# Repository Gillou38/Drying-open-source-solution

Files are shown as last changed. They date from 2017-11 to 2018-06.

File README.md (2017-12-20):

Open Source Vegetable Dryer
===========================

-   A vegetable dryer 

-   Combines solar and electrical energies

-   Designed for professional farmers

-   Scalable and autonomous

Motivation
----------

### Why this project?

This project is dedicated to farmers needing drying solutions for their
vegetables, aromatic or medicinal plants, fruits or other kinds of products. The
drying process allows farmers spreading their outcome beyond the harvest season
and therefore to secure a stable revenue over the year.

### Why open source?

We concur with the idea that open source and DIY farming tools support technical
independence, which is a critical issue for farmers. Therefore, dryer we want to
develop here is aimed to be open source, to be produced indifferently in DIY or
industrial production settings, and to be easily repaired. we are committed to
provide technical solutions with sufficient documentation securing the four
freedoms of open source:

-   Freedom to study: the right to access enough information to understand how
    the piece of hardware (referred herein as the product) works and to retrace
    the logic behind its design;

-   Freedom to modify: the right to edit the product definition documents and to
    tweak or develop the product further for any purpose;

-   Freedom to make: the right to use the product definition documents to
    manufacture the piece of hardware;

-   Freedom to distribute: the right to share or sell the product definition
    documents as well as the physical products fabricated according to these
    documents.

The documentation shared in this repository is licensed under a [GNU GPL v3
license](http://www.gnu.de/documents/gpl.en.html). Designs are licensed under a
[CERN Open Hardware Licence
V1.2](https://www.ohwr.org/licenses/cern-ohl/license_versions/v1.2).

### How to contribute

Every bit of help is more than welcomed. If you want to support the project,
promote it or concretely participate in the development, have a look at our
[Contribution
guide](https://github.com/Gillou38/Drying-open-source-solution/blob/master/Contribution%20guide.md)!

About dry-ing and -ers
----------------------

Drying is one of the most efficient food conservation methods. It helps keeping
a great share of nutriment, reduces the weight and the volume of food products
and enables long warehousing duration. It is a physicochemical reaction, whose
aim is to extract water out of something. Professional alimentary applications
requires dealing with conflicting constraints of high processing speed and
keeping control on the reaction in order to conserve valuable nutriments.

### History
That technic begins with the beginning of the agriculture, around 12 000 B. C. by inhabitants of the modern Middle East and Asia region. In beginning drying was realize by evaporation (air drying, sun drying ...). With time and technical evolution, there's actually a lot of different technic to dry food, from very low tech solution to high tech solution (we exclude freezing drying, because it's a very different process).

In drying, there is no “one-size-fits-all”-solution. Each farmer may need a very
specific solution fitting their specific requirements regarding size and
temperature range for example. The objective of the project is therefore to
develop a scalable and modular dryer which can be adapted to each specific
situation. Doing so, we want also to provide documentation about drying which
can be easily accessible to farmers.

### Composition of a dryer

A dryer is composed of:

-   a drying room, whose aim is to host the food products to be dried and to put
    their surface in contact with a dry and heated airflow. The role of the air
    flow is to capture the water contained in the food products while getting in
    contact with their surface. In order to maximise the contact surface, a good
    solution is to use trays helping to distribute the products and let the
    airflow circulating around them. Trays are generally made of food-safe
    screens and frameworks. For drying aromatic and medicinal plants, there are
    generally two ways to distribute products on the trays: the “thin layer”-way
    with only one layer of product on each tray, and the “thick layer”-way with
    around 10 to 15 centimetres of products on each tray.

-   a heating system, which can either be solar (direct or indirect), electrical
    or fuelled by biomass or combustion.

-   an air flow drying system, which can be either based on air exchange,
    condensation or absorption.

-   a convection system to convey the dry air flow through the drying room. The
    choice of the convection system depends on the product to be dried, the
    expected drying time and the thickness of the food's layer. It can be either
    natural or forced.

-   optionally a thermal inertia system, helping dryers whose heating system
    can't operate all day long (like solar systems) to stock energy.

Basic dryers tend to combine functions such as drying and heating into one
component and to use wind to create ventilation. More advanced solutions use one
component for each function.

Our design rationale
--------------------
We intend to use low tech and low energy consumption solutions whenever it is
possible. The current development focuses on a solar solution with electrical
assistance and regulation which enable professional users to process food
products regardless of the daytime (that is, even when there is no sunlight).

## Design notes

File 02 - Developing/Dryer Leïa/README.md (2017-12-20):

Dryer Model “Leïa”
==================

Specifications
--------------

Initial requirements

-   to dry 80kg of fresh herbs per week

-   drying time 2.5 days

-   40kg workload

-   thick layer loading (4 kg/m²)

Derived requirements

-   10m² drying surface

-   21 drawers of about 0,48m² (0,6\*0,8)

Materials
---------

-   Flat structures: resin-less OSB (oriented strand board)

-   Beams: pine

-   Drawer bottom: cheese maturing canvas

Supporting structure
---------

- Section: 50 x 50 mm
  
- No structure on the front side to tread drawers

- Fix together with angle connector

Drawers
-------

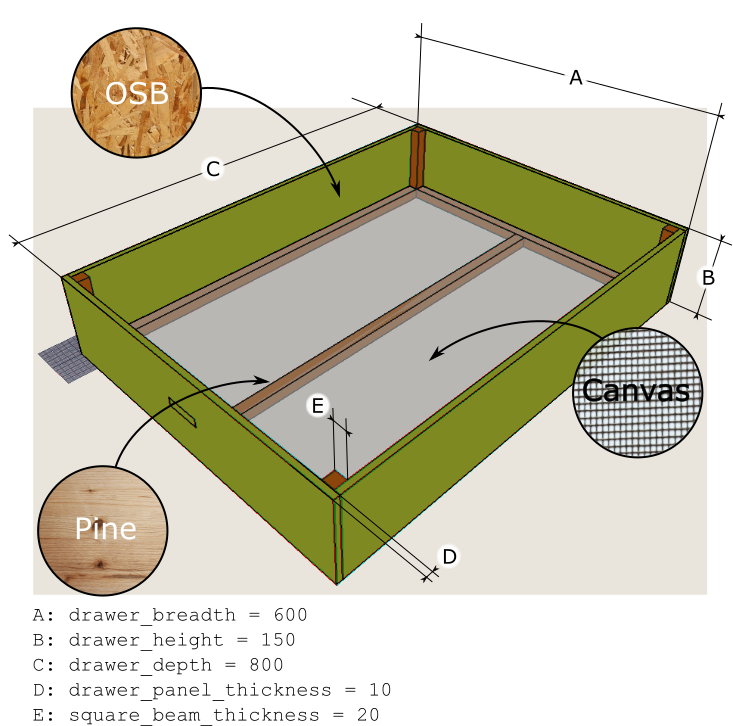
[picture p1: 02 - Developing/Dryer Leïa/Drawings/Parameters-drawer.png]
Drawer parameter sketch


Supporting structure
---------

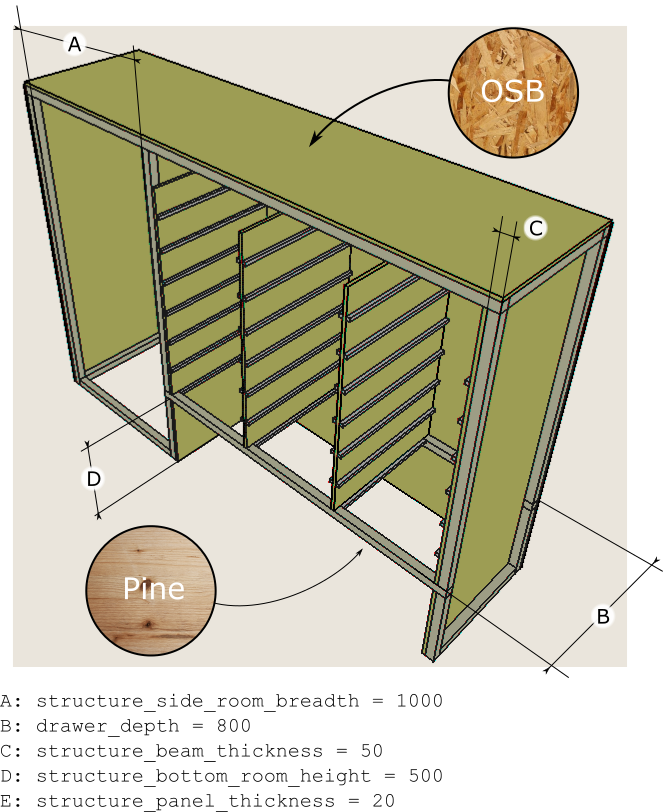
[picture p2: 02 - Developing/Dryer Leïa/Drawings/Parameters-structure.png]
Structure parameter sketch


Layout structure
---------

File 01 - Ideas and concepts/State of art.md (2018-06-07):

# State of art
#test
For basics category, we inspire by *“Les séchoirs solaires – Théorie et pratique”* de Michel Daguenet, because he made a huge work about drying science, and more applied to solar drying.

# Summary
## [Dryer for solid, centimetre scale](https://github.com/Gillou38/Drying-open-source-solution/blob/master/01%20-%20Ideas%20and%20concepts/State%20of%20art.md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)

### [Convective Dryer](https://github.com/Gillou38/Drying-open-source-solution/blob/master/01%20-%20Ideas%20and%20concepts/State%20of%20art.md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)

[1 Global parameter](https://github.com/Gillou38/Drying-open-source-solution/blob/master/01%20-%20Ideas%20and%20concepts/State%20of%20art.md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)

[2 Drying room](https://github.com/Gillou38/Drying-open-source-solution/blob/master/01%20-%20Ideas%20and%20concepts/State%20of%20art.md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)

[3 Suupling system](https://github.com/Gillou38/Drying-open-source-solution/blob/master/01%20-%20Ideas%20and%20concepts/State%20of%20art.md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)

[4 Heat source](https://github.com/Gillou38/Drying-open-source-solution/blob/master/01%20-%20Ideas%20and%20concepts/State%20of%20art.md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)

[5 Convection system](https://github.com/Gillou38/Drying-open-source-solution/blob/master/01%20-%20Ideas%20and%20concepts/State%20of%20art.md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)

[6 Automation](https://github.com/Gillou38/Drying-open-source-solution/blob/master/01%20-%20Ideas%20and%20concepts/State%20of%20art.md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)

[7 Alimentary legislation](https://github.com/Gillou38/Drying-open-source-solution/blob/master/01%20-%20Ideas%20and%20concepts/State%20of%20art.md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)

# Dryer for solid, centimetre scale
That part relate to drying of: 
- plants
- vegetables
- fruits
- nuts
- cheese
- mushroom
- more ?

For all that kind of food goods the process is almost the same, it use the same components (exept for cheese which doesn't need heating), only parameters change (temperature, time, relative humidity ...)

We try to make an inventory of all kind of dryer, and technology which could be used to dry, from the convective drying to the freeze drying, and defined each technology (electric, solar ...) used in each kind of dryers. For the 2nd level of category (convective, Freeze, IR, microwave) we choose to class them by kind of technology. Maybe, we can found a best classification.

## Convective drying
Convective drying consist of a contact between food goods and an heat and dry airflow to deshumidify food goods. It the most common process using for small products, because it's the cheaper and simpler process.

### 1. Global parameters
There is a lot of different kind of dryer, from the little dryer for domestic application to the huge dryer for industrial application, there can be organized in one block, or in some blocks, which make a more modulare system. 

#### A. Size
Actually we can’t precisely defined size in function of application, it depends of the food goods.
##### - Domestic
That’s kind of dryer could be used by a single man/women or a family for their own food.

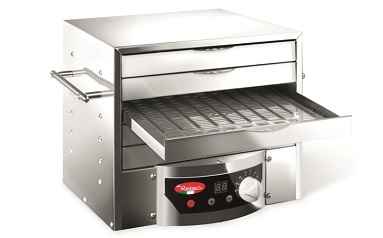
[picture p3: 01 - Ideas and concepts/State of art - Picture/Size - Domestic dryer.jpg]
Domestic dryer


##### - Little production
That size of dryer, is adapted to little company, people which want to sell product at local market.

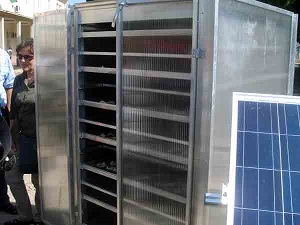
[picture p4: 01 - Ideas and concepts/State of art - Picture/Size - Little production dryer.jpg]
Little production dryer


##### - Industrial production
Dryer adapted for industrial production, sell product in large region.

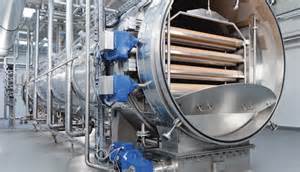
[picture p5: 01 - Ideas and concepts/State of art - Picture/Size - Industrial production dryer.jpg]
Industrial dryer


#### B. Organization
#####  - Mono-bloc
That kind of organisation could be a compact organization (like a multi-bloc organization hook together) or an all in drying room organization.

Advantages:
- easy to make, no pipe to link each part
- compact

Disadvantages:
- not transportable for middle size (size of a big wardrobe) of dryer

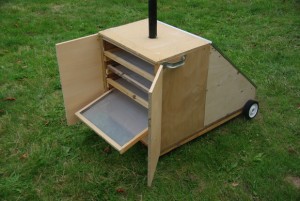
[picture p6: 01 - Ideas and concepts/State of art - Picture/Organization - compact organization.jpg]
Compact organization
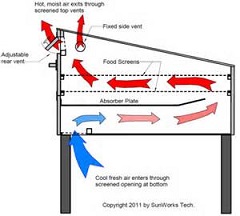
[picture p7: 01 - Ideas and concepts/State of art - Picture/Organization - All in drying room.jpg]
All in drying room
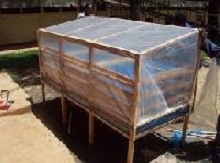
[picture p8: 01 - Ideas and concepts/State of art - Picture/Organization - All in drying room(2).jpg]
All in drying room (2)
           

#####   - Multi-bloc
Advantages:
- can be move by part, maybe can be taken apart (démonté)
- modulability

Disadvantages: 
- lost energy (temperature and airflow) in pipe

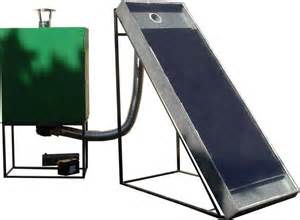
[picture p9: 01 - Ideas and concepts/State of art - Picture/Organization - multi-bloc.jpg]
Multi-bloc


#### C. Transportable
##### 1) Fixed
We don’t imaged that kind of dryer because it could defined by a very large panel of dryer. So we consider in that category all dryer which can’t be transport by 2 or less humans.
##### 2) Transportable
#####   - Portable
Defined by little dryer, which integrate handle or part which can be considered like handle, and which can be transport by maximum 2 peoples.

Portable

#####   - Pliable
The same restriction than a “portable” dryer, which pliable part to make an easy to transport dryer when it necessary.

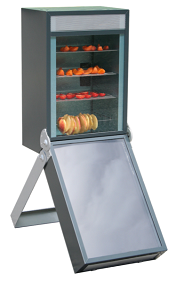
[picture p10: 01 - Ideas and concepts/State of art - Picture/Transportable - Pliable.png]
Pliable


#####   - Wheel
Dryer which integrate one or more wheel to transport it.

big one
2 Wheels

### 2. Drying room
#### A. Materials
We don't find European restriction for indirect contact, like it appear with drying room in a dryer. In that case, food goods can stay in the same room during few days with the same air, so we consider indirect contact like direct contact, we work later more presicely about that question. Maybe restriction could be simplified if the dryer work with renewable air.
(See under for more precision)

#### - Stone – Building:
Dryer directly integrate in a building. It can vary from old building (like an attic) to modern building with waxed concrete. For that part, we need to study food grade materials to identified what kind of material could be used, almost sure waxed concrete is legal, the rest need more study.

We think than, for nuts and that kind of fruit, dryer don't need to be totally clean, but for other kind of products building have to be really clean. 

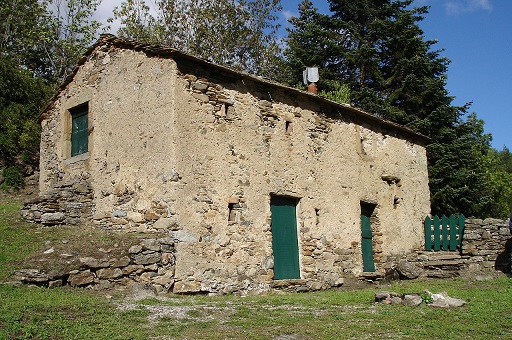
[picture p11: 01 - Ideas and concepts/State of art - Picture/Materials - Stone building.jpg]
Traditional nuts dryer


#### - Steel
Steel is a good solution for fruits and vegetables dryers, which need to be wash with water after each utilization, so stainless steel is easy to clean and it's resilient.

*[French source](http://www.contactalimentaire.com/index.php?id=204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)*

Stainless dryer

#### - Wood:
Wood is easiest material to make by oneself, but it doesn't work to any solutions, like with humid product (see under) which need to clean drying room with food grade cleaning product.

Wood dryer

#### - Plastic
Plastic is a good solution for fruits and vegetables dryers, which need to be wash with water after each utilization, so plastic is easy to clean but it isn't resilient.

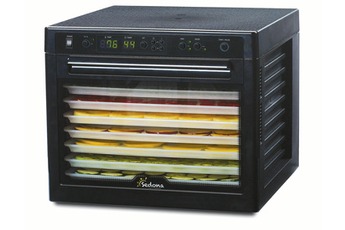
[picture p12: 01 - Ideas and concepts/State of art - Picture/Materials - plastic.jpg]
Plastic dryer


#### - Varnish materials
What kind of varnish could be used, what the maximum rate of product could be used.

- Vanish for wood
For fruit and vegetable dryers which need to be clean with water, wood without vanish can't reply to that restriction. So to vanish wood could be a great solution to have an easy to make dryer and respect very restricted alimentary regulation.

#### - cleaning products
You need to clean materials and objects, which could be in contact with food goods, before each using.

#### B. Shape
That the very hard part of the state of art, a lot of forms of dryer was experiment since the first realisation 12 000 years before, so we try to make the most complete list of kind of dryer, to inspire us and other to during the design of there dryer.
Maybe some dryers which can be regroup in the same category but to be sure to list all kind of dryer, we separate all little difference.
#### - Shell type (indirect solar natural convection)

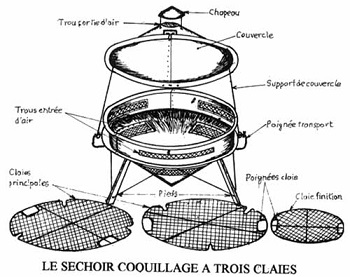
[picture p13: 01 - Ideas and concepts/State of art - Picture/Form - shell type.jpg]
Shell Type


#### - Vertical type with trays

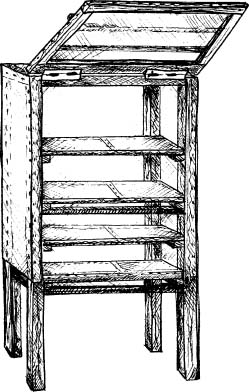
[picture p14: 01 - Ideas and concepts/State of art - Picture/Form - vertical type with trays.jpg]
Vertical with trays


#### - Spread type (solar direct):
Spread dryer, is a special form of vertical dryer, adapt to solar direct application, but it can be used in different case but that’s not real useful.

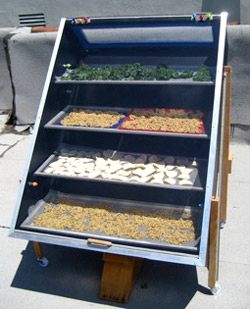
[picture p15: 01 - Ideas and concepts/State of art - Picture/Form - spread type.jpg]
Spread type


#### - Tunnel type
That’s more or less the same system than spread type, but for that category we exclude direct solar input. So, all kind of heat source could be considered. 

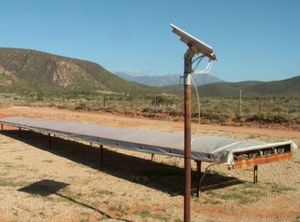
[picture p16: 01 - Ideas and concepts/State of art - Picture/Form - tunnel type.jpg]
Tunnel type
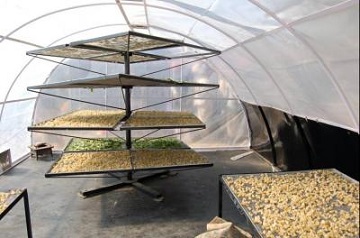
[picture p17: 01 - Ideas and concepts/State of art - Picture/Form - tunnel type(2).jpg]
Tunnel type(2)
     

#### - Rotative cylinder type
More adapted for cereals, and that kind of products. That kind of dryer is composed of a rotative drying room, which is crossed by an airflow. It provide to dry equitably all products. It doesn't need trays, but it need an high level of complexity. It more adapted for industrial applications.

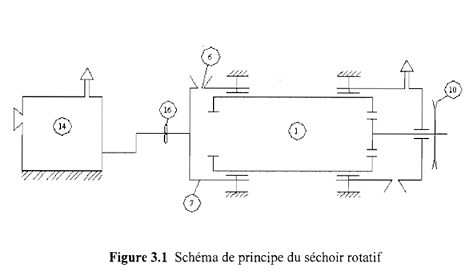
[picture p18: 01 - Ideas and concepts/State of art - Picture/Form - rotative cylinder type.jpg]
Rotative cylinder type
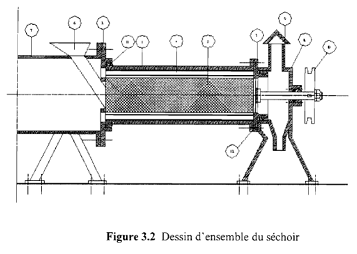
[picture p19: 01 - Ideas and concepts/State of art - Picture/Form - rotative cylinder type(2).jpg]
Rotative cylinder type
     

#### - Silo type

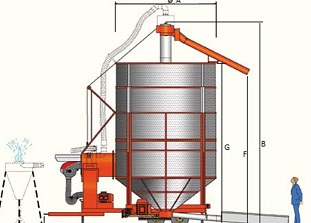
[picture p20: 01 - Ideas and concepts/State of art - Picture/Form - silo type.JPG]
Silo type


#### - Screw dryer type

screw dryer type

#### 3 Supplying systems
#### 3.1 Containing systems
Trays is the most using system to display product for artisanal or industrial application (exept for industrial drying of cereals), but other systems could be used in different applications.

For example, people who just want to dry some plants suspend bunch in an hot room ...

#### 3.1.1 Loosely

##### 3.1.1.1 Reversal
##### - Screw 
See [Screw dryer](http://www.amb-rousset.com/products/sechoir-a-vis/) or [another dryer](http://www.heinkel.com/products/dryers-and-mixers/conical-screw-vacuum-dryer.aspx)

##### 3.1.1.2 Not reversal

##### - Cylindric contener - Silo
Silo type

##### - Square contener - Bac

square contener

#### 3.1.2 Scatter

##### 3.1.2.1 Trays

Trays is most common solution for convective dryer, exept cereal dryer, which use bigger contener.

##### 3.1.2.1.1 Support

##### - Fabric
Maybe the best fabric solution is mosquito net (~7 €/linear meter) because, air can easy cross it, but verify alimentary application before.

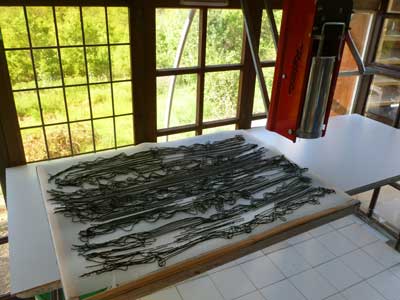
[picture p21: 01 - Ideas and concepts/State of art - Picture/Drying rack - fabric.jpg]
Tray with fabric


##### - Screen
Different kinds of screen could be used, for example:
- fine grillage: it isn't an alimentary material, verify regulation before to use something
- alimentary grille: generally using for oven or aging rack
- ripening mat for cheese: that's a good solution because, it make for alimentary application so, there isn't problem with respect of regulation. Exist in different materials: plastic, inox

Fromagex - ripening mat
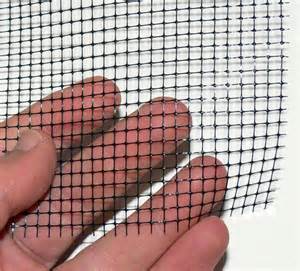
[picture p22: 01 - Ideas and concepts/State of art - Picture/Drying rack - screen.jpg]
Fine grillage

alimentary grille

##### 3.1.2.1.2 Spread thickness
For plant drying you can choose to spread it by thick layer, you need to adapt the system for that kind of spreading, avoid pressure loss.
For cutted fruit and vegetable, you need to spread product in thin layer.

##### - Thin layers
Adavantage:
- work with natural convection

Disadvantage:
- long time of supplying

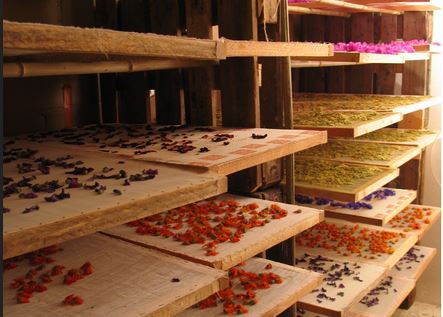
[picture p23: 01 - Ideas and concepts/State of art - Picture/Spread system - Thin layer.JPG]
Thin layer


##### - Thick layers
Adavantage:
- easy to supply

Disadvantage:
- pressure loss (need forced convection)

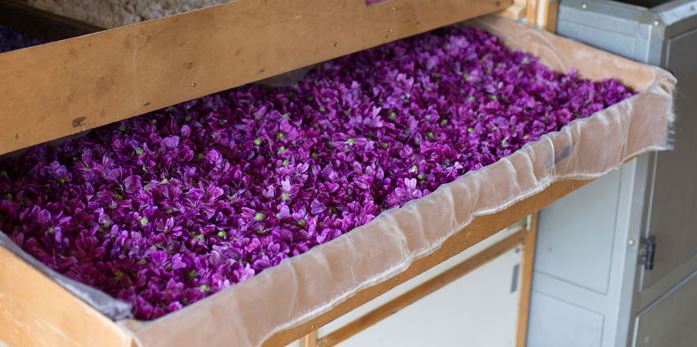
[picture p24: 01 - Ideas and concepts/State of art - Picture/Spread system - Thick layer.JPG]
Thick layer


##### 3.1.2.2 Bar
That kind of display is more adapt to long product or to plant bunch.
Bar    Bar(2)

##### 3.1.2.3 Pic
Maybe with that technic, you can dry more fruit or vegetable than with trays, but it need more time to spread them.



##### 3.1.2.4 String
More adapted for plant bunch, you can tie plant together and suspend them. It's a very tedious technic but which doesn't need any construction.

Plant bunch

#### 3.2 Loading systems

##### 3.2.1 Manual - 

##### 3.2.1.1 Slide system

##### 3.2.1.1.1 Perpendicular to the door
##### - Rail
Like for storage drawer

Rail

##### - Angle iron
Angle iron

##### - Wood batten
Wood batten

##### 3.2.1.1.2 Parallel to the door

##### - Bambou
Thin layer

##### 3.2.1.2 Roll system

##### - Cart - Mobile trays

Mobile trays

##### 3.2.1.3 Hang system

##### - Hook

##### - Knot
Plant bunch

##### - Elastic

##### 3.2.1.4 Distribut system

##### 3.2.2 Automatic

##### 3.2.2.1 Distributor system
Pipe with electrical valvle
Distibutor system

##### 3.2.2.2 Conveyor system
##### - Cart conveyor
Cart conveyor

##### - Conveyor belt
Conveyor belt

##### 3.2.2.3 Endless srew system
Endless srew

##### 3.3 Spreading system

##### 3.3.1 Manual

##### 3.3.2 Automatic

##### - Equaliser

Equaliser

##### - Vibration

### 4. Heat source
Heat source is one of technical problem of dryer. Between effectiveness and energy independence, there is a real work to search what kind of heat source to what kind of application, to optimize known heat source and to mix some kind of heat source.

Maximal temperature depend of the product. Some tables indicate temperature and time to each products.

### A. Solar (warm and non pollute flow)
Solar heating is maybe the simplest system to dry food goods, but you really dependant of sunray. Generally, drying is practice during good season, but a session last more than one day, so drying stop during the night. 
### Kind of caption
#### - Direct:
The most simple application for solar energy, sun heat directly the product. Generally, heating across a transparent film, to using greenhouse effect to increase temperature, but sunray destroy some of nutritive components of the product.
You can also do it without transparent film.

Solar direct

#### - Indirect:
It consist to using solar thermal panels, link to the drying room.

##### - Glassed
In that system, sunray cross glass before heat a dark plate. After greenhouse effect increase temperature in the panel. Simply, the system can be a box with one side glassed.

To optimize it:
- double glazing: it increase greenhouse effect and isolation of the system. To optimize double glazing insolation, you can increase distance between glasses until 4mm. After a convective in space between the glasse reduce isolation.
- darkest plate: it increase absorption sunray. for greenhouse effect, we need to have the sunray which can't cross glassed when they're inside the box. Dark material modify frequency of sunray. With there new frequency they more block in the panel.
- external isolation: it increase temperature conservation in the box

To size your solar panel:
- For plant, you need nearly third of meter square of panel of the weight of your production.
- for fruits and vegetables:
- ...

Solar indirect glassed    
Solar indirect glassed(2)

##### - Opaque

Solar indirect opaque    Solar indirect opaque(2)    Solar indirect opaque(3)     Solar indirect opaque(4)     Solar indirect opaque(5)

##### - Mixed (direct + indirect)

Solar mixed)

#### Other parameters
##### - Positioning
- Azimuth
- Normal of the ground
##### - Inertial system (conservation of energy)
- Stone 
Inertial system)

#### Other kinf of panel
##### Hybrid Panel PV/T (Photovoltaic and Thermical panel

http://www.sft.asso.fr/Local/sft/dir/user-3775/documents/actes/congres_2011/Communications/133.pdf
http://manifest.univ-ouargla.dz/documents/Archive/2015-2016/FSA/SMSTS%202015/SMSTS-2015_Soumission_n%c2%b047.pdf

#### B. Electrical (resistor)

Electrical)

dehumidifer Trotec

#### C. Warm and pollute flow
That kind of heat source need a heat exchanger to separate pollute flow and drying flow.
#### Heat exchanger 
(source: http://www.uk-exchangers.com/heat-exchange-products/air-to-air-heat-exchangers/)
Different kind of heat exchanger can be used to transfer energy from 1st fluid to a 2nd fluid. For beginning, we stay only in airflow exchanger.
##### - Plate type

Plate type)

##### - Thermal wheel type

Thermal wheel type)

##### - Tubular type

Tubular type)

#### Heat source
- Compost

- Oil combustion

- Wood combustion
Wood combustion

### 5. Convection
#### A. Kind
There is 2 kind of airflow creation using in dryer:
- natural convection: the airflow isn't pulsed
- forced convection: the airflow is pulsed by an additional system

##### Natural convection
It Work with rising warm airflow, so the airflow isn't pulsed by an additional system.

So that kind of system generally use the natural caracteristic of warmflow to go up.

That's a very simple system to make but it can't be regulate to improve drying, or just to avoid too high temperature with increase airflow.

Natural convection

##### Forced convection
Forced convection consist of a system which pulse airflow, to increase speed of drying, principally for 2 reasons.
- For a professionnal application, producer need to have bigger production to respond to there financial need
- With decrease of drying time, nutrient concentration increase. Drying is a physical chemistry reaction which deteriorate nutrient, so the faster is the best, but the faster need more energy.

##### - Electrical

That's the more common solution for professional application, more expensive and complicated to make, with that kind of system, you can regulate the drying.

Forced convection - electrical

##### - Wind forced
That kind of system is autonomous in energy, but it need to have access to wind and can't be regulate.

Forced convection - wind

#### B. Direction
In that part we only speak for trays, in other kind of system, direction of the convection could be different.

##### Perpendicular to the trays
The more common system use in DIY system because the easiest system to make and that work for each kind of product.

Convection perpendicular to the trays

##### Bottom up

##### Up bottom

##### - Air repartition (plenum)
- Air flow breaker

Air flow breaker

- Room distributor
	
Room distributor

##### Parallel to the trays
Only use for thin layer (all cutted fruit and vegetable, thin layer of plant), it's the most efficient choice because it divide warm airflow in all product and it limit pressure loss.

Parallel to the trays Parallel to the trays   Parallel to the trays   Parallel to the trays

### 6. Dehumidifier 
#### A. Opened pipe - Air exchange
- Complete renewal of air

complete renewal of air
	
- Partial renewal of air

Good choice of pipes' diameter (Benaouda and al.)
Partial renewal of air

#### B. Closed pipe

You can find a dehumidifier with a ventilation system. That's make a complete system to dry. Easy to instal and run, but you can't adjust it like you want. Generally, only one button to adjust all parameters. That's the simplest solution but not the more precise. If you out it in a little box, it could to heat too much, so you need to stop the system (manually or automatically).

- Condensation

Condensation

- Absorption

Absorption

### 6. Automation

### 7. Alimentary legislation

We can distinct 2 kind of using material in a dryer:
- Direct contact: materials wich be in a direct contact with food goods. For example, the trays or other kind of spreading have a direct contact with food goods. So for that kind of restriction there is European restriction about that which integrate certain restriction for each kind of materials (plastic, wood ...)
- Indirect contact: materials which don't have direct contact, like the drying room, but have a direct contact with airflow. For that kind of materials, there is a difference between plant (maybe cereals too) and fruit and vegetable, by the difference of humidity and sugar, in the product. In the 1st hand, it need only to clean dust, and in the other hand, it need to clean eventual  caramel on the side.

#### Direct contact
The best way to respect restriction is to use food grade product, but we try to popularize restriction to divert other material and products.

European laws indicate regulation for direct contact, so there isn't direct contact with nuts, they don't need food grade materials.(verify that information)

For direct alimentary contact, it need to respect [European regulation](http://www.europarl.europa.eu/RegData/etudes/STUD/2016/581411/EPRS_STU%282016%29581411_EN.pdf) which identify inertia of the material. It depend of:
- materials composition
- migration's treshold in food goods, of substance which composed materials
- lack of deterioration of organoleptic properties (taste, smell, sight and touch) by materials

There is specific criteria for:
- materials which could be treat (ionization, recycling ...) 
- coloring materials
- cleaning product using on material which have contacte with good foods

#### Steel
Steel is a good solution for fruits and vegetables dryers, which need to be wash with water after each utilization, so stainless steel is easy to clean and it's resilient.

Like it's precise before, for each kind of material there is special restriction about there inertial ctriteria.
Inertial criteria to respect are:
- chemical composition ([European laws in french](http://www.contactalimentaire.com/fileadmin/ImageFichier_Archive/contact_alimentaire/Fichiers_Documents/Brochure_JO/Note_2004_64/Fiches_DGCCRF_Revisees/DGCCRF-Fiches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)
- limit of undesirable elements:
	- Lead (Plomb): < 0.05 %
	- Cadmium: < 0.01 %
	- Arsenic: < 0.03 %
	- ...
- specific migration of metalic element :
	- Nickel < 0.5 mg/kg of food goods
	- Chrome < 5 mg/kg of food goods
	- Zinc < 10 mg/kg of food goods
	- Lead < 4 mg/kg of food goods
	- cadmium < 0.3 mg/kg of food goods
	-...

#### - Wood:
For European regulation, 2 categories of criteria could influence the choice :
- wood variety:
	- accept all food goods: oak, sweet chestnut, ash, hornbeam, black locust, pine, spruce, douglas, maritime pine, scotch pine, poplar, beech, plane, aspen, alder, olive, birch
	- only for solid food goods: walnut, elm, 
- essence de bois: 
	- pour tout les aliments : chêne, châtaignier, frêne, charme, robinier, sapin, épicéa, douglas, pin maritime, pin sylvestre, peuplier, hêtre, platane, tremble, aulne, olivier, bouleau
	- pour les solide alimentaires : hêtre, noyer, orme, peuplier
- wood treatment: 
	- no pentachlorophenol treatment (< 0,1 mg/kg of wood)
	- ?
- traitement du bois : 
	- Absence de traitement au pentachlorophénol (< 0,1 mg/kg de bois)
	- Produits de traitement autorisés pour les emballages de fruits et légumes

*[french source](http://www.contactalimentaire.com/index.php?id=382)*

#### - Plastic
Plastic is a good solution for fruits and vegetables dryers, which need to be wash with water after each utilization, so plastic is easy to clean but it isn't resilient.
Inertial criteria to respect is decompose of 3 categories:
- global restriction about substances
- global limit of migration: < 10 mg/dm² (for material which used to babies good foods (< 3years), the limit is 60 mg/dm²)
- specific limit of migration

*[French source](http://www.contactalimentaire.com/index.php?id=250), and [other](http://www.contactalimentaire.com/fileadmin/ImageFichier_Archive/contact_alimentaire/Fichiers_Documents/autres/Fiches-materiaux-organiques-matieres-synthetiques.pdf)*
*[epoxy document](http://www.contactalimentaire.com/fileadmin/ImageFichier_Archive/contact_alimentaire/Fichiers_Documents/Reglements_anglais/reg2005-1895ang.pdf)*

#### - Varnish materials
What kind of varnish could be used, what the maximum rate of product could be used.

- Vanish for wood
For fruit and vegetable dryers which need to be clean with water, wood without vanish can't reply to that restriction. So to vanish wood could be a great solution to have an easy to make dryer and respect very restricted alimentary regulation.

#### Indirect contact

Restriction about indirect contact is about cleaning material we can distinct 2 kind of product:
- humid products: like fruit and vegetable which need to be clean with liquid product after each utilisation. Indeed humid material dirty the interior of the drying room because of high level of sugar or other component in airflow.
- other products: like plant and cereal which need to clean dust in the dryer.

#### - Varnish materials
What kind of varnish could be used, what the maximum rate of product could be used.

- Vanish for wood
For fruit and vegetable dryers which need to be clean with water, wood without vanish can't reply to that restriction. So to vanish wood could be a great solution to have an easy to make dryer and respect very restricted alimentary regulation.

### 8.Electrical restriction
Tout les composants d’entrée

- Classe IP 44 ? humidity restriction for electrical components

## IR drying

## Microwave drying

## Freeze drying

# Dryer for solid, metre scale (wood)
- Wood solar dryer
Notice for one : https://pubs.ext.vt.edu/content/dam/pubs_ext_vt_edu/420/420-030/420-030_pdf.pdf

other state of art :
https://www.stejarmasiv.ro/uscator-de-lemn-solar/
https://www.builditsolar.com/Projects/WoodDrying/wood_kiln.htm

Wood dryer
Wood dryer

# Dryer for pumpable product (liquid, dought …)

## Conductive drying

# Dryer for powedered product (crumbled vegetables, pulp, cereals ... )

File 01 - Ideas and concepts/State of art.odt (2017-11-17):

State of art

For basics category, we inspire by “Les séchoirs solaires – Théorie et pratique” de Michel Daguenet, because he made a huge work about drying science, and more applied to solar drying.

Dryer for solid, centimetre scale

That document try to make an inventory of all kind of dryer, and technology which could be used to dry, from the convective drying to the freeze drying, and defined each technology (electric, solar ...) used in each kind of dryers. For the 2nd level category (convective, …) we choose to class them by kind of technology. Maybe, we can found a best classification.

Convective drying

1. Global parameters
  There is a lot of different kind of dryer, from the little dryer for domestic application to the huge dryer for industrial application.

### A. Size

Actually we can’t precisely defined size in function of application, it depends of the food goods.

- Domestic

That’s kind of dryer could be used by a single man/women or a family for their own food.

- Little production

That size of dryer, is adapted to little company, people which want to sell product at local market


- Industrial production

Dryer adapted for industrial production, sell product in large region.

### B. Organization

- Mono-bloc
  That kind of organisation could be a compact organization (like a multi-bloc organization hook together) or an all in drying room organization
  Advantages:
- easy to make, no pipe to link each part
- compact

Disadvantages:

- not transportable for middle size (size of a big wardrobe) of dryer

Retour sur lâ atelier de fabrication dâ un sÃ©choir solaire ...

Illustration 1: Compact organisation

Illustration 2: All in drying room organization (1)


Illustration 3: All in drying room organization (2)

- Multi-bloc
  Advantages:
- can be move by part, maybe can be taken apart (démonté)
  Disadvantages:
- lost energy (temperature and airflow) in pipe


Illustration 4: Multi-bloc organization

2. Transportable
    a. Fixe

We don’t imaged that kind of dryer because it could defined by a very large panel of dryer. So we consider in that category all dryer which can’t be transport by 2 or less humans.

    a. Transportable
- Portable
  Defined by little dryer, which integrate handle or part which can be considered like handle, and which can be transport by maximum 2 peoples.
- Pliable
  The same restriction than a “portable” dryer, which pliable part to make an easy to transport dryer when it necessary.
- Wheel
  Dryer which integrate one or more wheel to transport it.

Illustration 5: 2 wheels integrated dryer

3. Drying room

### Materials

- Stone – Building :

Dryer directly integrate in a building. It can vary from old building (like attic) to modern building with waxed concrete. For that part, we need to study alimentary laws to identified what kind of material could be used, almost sure waxed concrete is legal, the rest need more study.

Illustration 6: Séchoir traditionnel français à chataignes

- Steel
  The same than the precedent category for metal dryer. What kind of metal can be used, some stainless steels for sure, very probably some aluminium, but need more study to identify them precisely.

Illustration 7: Stainless steel dryer by Reber company

- Wood:
- Plastic

Tout le choix Darty en Déshydrateur / stérilisateur | Darty

- Varnish materials

What kind of varnish could be used, what the maximum rate of product could be used.

### Form

That the very hard part of the state of art, a lot of forms of dryer was experiment since the first realisation 12 000 years before, so we try to make the most complete list of dryer.

- type shell (indirect solar natural convection)


- type vertical with trays

- type spread (solar direct):

Spread dryer, is a special form of vertical dryer, adapt to solar direct application, but it can be used in different case but that’s not real useful.


- type tunnel

- type rotative cylinder


4. Trays
- Fabric


- Screen
- Pic
5. Heat source
    a. Solar (warm and non pollute flow)
- Kind of caption
  - Direct:

Etude, conception, réalisation et expérimentation d’un ...

  - Indirect:


    - Glassed
    - Opaque

L'ATELIER des COUREURS des BOIS: Fabrication d'un sÃ©choir ...

  - Mixed (direct + indirect)


- Positioning
  - Azimuth
  - Normal of the ground
- Inertial system (conservation of energy)
  - Stone
    a. Electrical (resistor)

Tre Spade Benchtop Dehydrators

### Warm and pollute flow

That kind of heat source need a heat exchanger to separate pollute flow and drying flow.

- Heat exchanger

(source: http://www.uk-exchangers.com/heat-exchange-products/air-to-air-heat-exchangers/)

Different kind of heat exchanger can be used to transfer energy from 1st fluid to a 2nd fluid. For beginning, we stay only in airflow exchanger.

  - Plate type
  - Thermal wheel type
  - Tubular type


- Heat source
  - Compost
  - Oil combustion
  - Wood combustion
6. Convection
    a. Kind
- Natural: Work with rising warm airflow


- Forced
  - Electrical
- Wind forced


    a. Direction
- Perpendicular to the trays

Four et sÃ©choir solaire - Jardins en partage

- Air repartition (plenum)

- air flow breaker

- room


- Parallel to the trays
  7. Dehumidifier

### Opened pipe

- Air exchange

### Closed pipe

- Condensation


- Absorption

7. Alimentary legislation

Contact alimentaire direct

- claie

Contact alimentaire indirect

Tout les composants d’entrée

Conductive drying

IR drying

Microwave drying

Freeze drying

Dryer for solid, metre scale (wood)

- Wood solar dryer


Dryer for pumpable product (liquid, dought …)

Dryer for powedered product (crumbled vegetables, pulp, cereals ... )

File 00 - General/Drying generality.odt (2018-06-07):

Convective drying generality

Farmer point of view

(source : fiche technique – séchage – Sébastien Bonduau (CAB) et Thibault Joliet (CFPPA de Montmorrot – juin 2013)

Principe : extracion de l'eau contenue dans la plante

La plante

- Humidité de la plante avant séchage : entre 70% et 90%

- L'eau à extraire se trouve dans chaque cellule de la plante et doit donc migrer à sa surface pour s'évaporer

- Il existe des forces superficielles qui retiennent l'eau dans la plante, elles sont très faible lorsque l'eau est abondante, elles deviennent de ples en plus fortes au fur et à mesure que la disponibilité de l'eau diminue

L'air

- composé d'air sec et de vapeur d'eau

- se caractérise par sa température (T°C) et son taux d'humidité relative (HR%)

- sa capacité à se charger en eau dépend de sa température. Un air à 20°C et à 60% d'humidité contient 10,5g/m3 de vapeur d'eau, une air à 35°C et 60% d'humidité contient 24g/m3 de vapeur d'eau

- Le taux d’humidité relative est le pourcentage de vapeur d’eau contenu dans un m3 d’air par rap-port au maximum que ce même m3 peut contenir à la même température.

- L’humidité absolue est la quantité totale de vapeur contenue dans l’air elle peut s’exprimer en g/m3.

La durée du séchage

- Elle varie en fonction du taux d’humidité et de la présentation ou granulométrie du produit à sé-cher, de l’humidité relative et de la température de l’air, du volume d’air passant par les plantes (ventilation).

- Elle ne devrait pas dépasser 5 jours.

- Elle n’est pas compressible en dessous d’un certain seuil à moins de travailler à haute température (6 h à 12 h pour une fleur type mauve, 48 h pour une partie aérienne, non découpée, type menthe).

Dimensionnement d'un séchoire solaire

Le raisonnement est le suivant : « Je souhaite produire X kg de plante sèche à l’année, avec telle présentation et j’attends telle qualité de séchage. J’ai un pic d’activité sur tel mois de l’année où je dois sécher Y kg de plante par semaine, j’ai donc besoin de Y mètres carrés de claies.

- Je souhaite travailler avec un déshumidificateur, je choisi un appareil avec une capacité de déshumidification d’au moins Y litres/24h et une ventilation la plus importante possible, je dimensionne mon ventilateur par rap-port à la ventilation de mon déshumidificateur en tenant compte des pertes de charges dans le circuit.

- Je souhaite travailler avec des capteurs solaires, j’ai besoin de Z = (Y/3) m² de capteur, je calcul ma ventilation pour arriver à une vitesse de circulation de l’air comprise entre 2 et 5 m/s en tenant compte des pertes de charge dans le circuit.

- Je souhaite travailler avec un système de chauffage de l’air ambiant, je compte 1kW de puissance pour 30 kg de capacité de chargement avec une ventilation comprise entre 200 et 500 m3/h en tenant compte des pertes de charge dans le circuit.

Engineer point of view

Scientist point of view

# Courbe caractéristique de séchage


Flux évaporé

Humidité absolue de l’air

# Moist Air

(source : Les séchoires solaires – Théorie et pratique – Michel Daguenet - UNESCO – p431)

Air humide : mélange d'air sec et de vapeur d'eau.

Soit une masse d'air humide, m, occupant à la température T(°K) un volume V sous une pression totale P. On a :

P = somme (Pi) avec Pi = (ni * R * T)/V (loi de Dalton et loi des gazs parfaits)

et

rho = somme (rhoi) avec rhoi = mi/V

où mi = masse du gaz i dans le mélange

rho = masse volumique du mélange

ni = nombre de moles du gaz

Posons :

mv = masse de vapeur dans le volume V du mélange

mas = masse d'air sec dans le volume V du mélange

m = mv + mas

rhov = masse volumique de la vapeur

rhoas = masse volumique de l'air sec

rhovs = masse volumique de la vapeur saturée

# Moist body

## - les différents mode de liaison de l'eau

(source : Les séchoires solaires – Théorie et pratique - Michel Daguenet - UNESCO - p443)

Les corps contenant de l'eau sont classé suivant la nature des liaisons entre l'eau et les autres composants, pour l'opération de séchage, il faut enlever toute l'eau du corps, dite humide, et non son eau d'hydratation :

- corps hydraté : liaison très forte (par association de molécule) et ? (inséré dans un réseau cristallin), pour enlever l'eau il faut détruire le corps. Cette opération ne nous intéresse pas ici.

- corps humide : retenu sur la surface du corps par des forces d'attraction de surface, d'origine moléculaire et de type Van der Waals :

- 1ere couche : phénomène d'absoption, fortement retenu et la force diminue rapidement quand on s'éloigne de la surface vers l'extérieur du corps

- 2ème couche : phénomène d'osmose

- 3ème couche : phénomène mécanique

## - humidité relative et absolue

- Humidité relative : x = (m – ms) / m

- humidité absolue : X = (m – ms) / ms

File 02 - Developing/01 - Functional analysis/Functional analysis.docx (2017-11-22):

# Functional analysis

## Functional analysis

- Function: a function is an action, a service or a constraint of a product
- Interactor: all element which have a contact or a relation with the product
- Phase: different using phase (using phase, supplying phase, cleaning phase …)

To find product’s functions, generally it needs to identify all interactor, and to identify all interactors it need to identify the using phases.

### Different phases

For that product, we imagine 6 different phases. Except the 2 main phases, the utilisation phase and the supplying phase, all of other phases is optional and we tried to developed a product which can integrate, or not, that phase, according to user’s desire.

The different phases are:

- Drying phase
- Cleaning phase
- Supplying phase
- Stocking phase
- Transport phase
- Maintenance phase

### Drying phase

#### Product/Interactors/Functions - Schematic links:

User

Food

External energy

External environment

Dryer

Legislation

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
#### Interactor characterisation:

Kind of interactor | Interactor | Criterion | Level
User | - | Size Muscular capacity
| Professional | Technical level
| Amateur
Food | Vegetables, moist food | Relative humidity Size Capillarity T° max
| Aromatics and medicinal plants
| Cheese
| Nuts
| Meat
| Cereal
External energy | Electricity | Power
| Non pollute flow Solar
| Pollute flow Combustion/compost
Legislation | French legislation
External environment | Building – house | Meteo T ext
| Outside

#### Function characterisation

The dryer need to:

- Principal function:
  - PF1: Dry dietary products
- Using function:
  - UF1: Be ergonomic
  - UF2: Contain food - Capacity (kg/week producer units, transfer it in technician units)
  - UF3: Respect alimentary laws - Material choice
  - UF4: drying speed – optimisation of the heating and airflow drying
  - UF5: drying homogeneity – optimisation of convection
- Constraint function:
  - CF1: Product quality (T° regulation)
  - CF2: Noise pollution

Function | Criterion | Level | Limit | Flexibility
PF1 : Dry | T° mini
| Humidity/s
| Speed flow
UF1: Ergonomic | Time to prepare a session
| Time during a session
| Technical level
UF2: Capacity | Kg/week
UF3: Alimentary laws | Contact direct
| Contact indirect (by flow)
UF4: Drying speed | Regulation of heating
| Regulation of airflow
UF5: Drying homogeneity | Repartition of the airflow
CF1 : product quality | T° limit
| Nutriment saturation in the airflow
CF2: Noise pollution | Noise

Fast for lists of solution

- Detailed of that function in technical solutions on Using phase/FAST document

SADT for choice of solution

- Comparison of function on Using phase/SADT document

### Supplying phase

User

Food

Dryer

PF1

- PF1: be simple to supply and to empty food

### Cleaning phase

- PF1: Be washable

### Stocking phase

- PF1: Take a minimum of place

### Transport phase

- PF1: Be transportable

### Maintenance/optimisation phase

- UF1: Be reparable
- UF3: Be adaptable to different kind of product

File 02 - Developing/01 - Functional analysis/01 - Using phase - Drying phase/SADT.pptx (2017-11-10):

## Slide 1

Food dryer
SADT – A0 level

User interaction

Food dryer

Humid food

Dry food

Energy

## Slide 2

Food dryer
SADT – A-0 level

User action

Humid food

UF3: Contain food

PF1: Dry food

Dry food

Cold air

UF2: Be ergonomic

Energy

## Choice of order of Principals Functions

A-0 level

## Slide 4

PF1: Dry dietary products
Solution 2: Create airflow after produce heat

Humid products

Prepare product
Trays
Pique
In a jumble

TF5: Create interaction between dry airflow and humid products
Shell
Vertical
Spread
Tunnel
Cylinder

Exterior action

PF1: Dry dietary product

TF1: Produce heat
Solar
Electric
Combustion/compost

Warm airflow

TF2: Create an airflow
Natural Convection
Forced Convection

TF3: Dry airflow
Air exchange
Absorption
Condensation

Dry and cold airflow

Warm airflow pulsed

Humid airflow pulsed

Dry products

Energy

Get product out

Dry products to pack

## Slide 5

PF1: Dry dietary products
Solution 2: Create airflow before produce heat

Humid products

Prepare product
Trays
Pique
In a jumble

Humid products to dry

TF5: Create interaction between dry airflow and humid products
Shell
Vertical
Spread
Tunnel
Cylinder

Exterior action

PF1: Dry dietary product

TF2: Create an airflow
Natural Convection
Forced Convection

Warm airflow

TF1: Produce heat
Solar
Electric
Combustion/compost

TF3: Dry airflow
Air exchange
Absorption
Condensation

Dry and cold airflow

Warm airflow pulsed

Humid airflow pulsed

Energy

Get product out

Dry products

Dry products to pack

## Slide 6

PF1: Dry dietary products
Solution 3: Create airflow after drying room

Humid products

Prepare product
Trays
Pique
In a jumble

Exterior action

PF1: Dry dietary product

TF1: Produce heat
Solar
Electric
Combustion/compost

Humid products to dry

TF5: Create interaction between dry airflow and humid products
Shell
Vertical
Spread
Tunnel
Cylinder

TF2: Create an airflow
Natural Convection
Forced Convection

TF3: Dry airflow
Air exchange
Absorption
Condensation

Dry and cold airflow

Warm airflow pulsed

Warm airflow

Humid airflow pulsed

Dry products

Energy

Get product out

Dry products to pack

## Choice of order of functions

We eliminate other solutions by logic.

- Solution 1
- Create airflow after produce heat

- Advantages
  - Good control of airflow in the drying room
- Disadvantage
  - Strong pressure, need a component to divide it (plenum)

- Solution 2
- Create airflow after produce heat

- Advantages
  - Best airflow repartition at the enter of the drying room
- Disadvantages
  - Hard to optimisable

Solution 3
Create airflow after drying room

Advantages
Easy to use with wind ventilator
Disadvantages
Hard to optimisable

## Choice of components

A-1 level

## TF1: Produce heat Solution 1 : solar heating

TF1: Produce heat

Cold air

Transfer warm in airflow
Plane
Chicane
Fin

Thermal energy

Transfer solar energy to warm
Black body

Solar energy

Warm air

Focus warm air
Tunnel
Box

Possible of warm airflow

## TF1: Produce heat Solution 2: electrical heating

TF1: Produce heat

Cold air

Transfer warm in airflow
Plane
Fin

Thermal energy

Transfer electrical energy to warm
Resistor

Electrical energy

Warm air

Focus warm air
Tunnel / pipe
Box

Possible of warm airflow

## TF1: Produce heat Solution 3: Solid combustor (wood …)

TF1: Produce heat

Cold air

Transfer warm in airflow
Plane
Fin

Thermal energy

Transfer warm in solid
Plane
Fin

Warm air

Focus warm air
Tunnel / pipe
Box

Usable air

Warm and unusable air

Cold air

Burn wood

Create convection

Warm and unusable airflow

Cold and unusable flow

Wood

## TF1: Produce heat Solution 4: Fluid combustor (oil, biogas, ethanol …)

TF1: Produce heat

Cold air

Transfer warm in airflow
Plane
Fin

Thermal energy

Transfer warm in solid
Plane
Fin

Warm air

Focus warm air
Tunnel / pipe
Box

Possible of warm airflow

Warm and unusable air

Cold air

Burn oil

Create convection

Warm and unusable airflow

Cold and unusable flow

Oil

## TF1: Produce heat Solution 5: Compost

TF1: Produce heat

Cold air

Transfert warm in airflow
Plane
Fin

Thermal energy

Transfert warm in solid

Warm air

Focus warm air
Tunnel / pipe
Box

Possible of warm airflow

Transfert warm in flow

Warm and pollute flow

Cold and pollute flow

## Choice of heat producer

- Solution 1
- Solar

- Advantages
  - Easy to construct
  - Low-cost
  - Easy to repair
  - Easy to be autonomous
  - Renewable
  - Simple to use
- Disadvantage
  - Usable only during day

- Solution 2
- Electric

- Advantages
  - Easy to construct
  - Low-cost
  - Easy to change
  - Simple to use
- Disadvantages

Solution 3
Wood combustor

Advantages
Easy to be autonomous
Renewable
Simple to use
Disadvantages
Complex to construct

## Choice of heat producer

- Solution 4
- Oil combustor

Advantages
Simple to use
Disadvantages
Complex to construct

- Solution 5
- Compost

- Advantages
  - Renewable
  - Easy to be autonomous
- Disadvantages

## TF2: Create an airflow Solution 1: Warm in draught

TF2: Create an airflow

Make a depression

Usable air

Warm airflow

Guide airflow

Usable airflow

## TF2: Create an airflow Solution 2: Wind in draught

## TF2: Create an airflow Solution 3: Electrical ventilator

TF2: Create an airflow

Pulse air

Usable air

Usable airflow

Electrical energy

## TF2: Create an airflow Solution 4: Wind ventilator

TF2: Create an airflow

Pulse air

Usable air

Usable airflow

Wind energy

## Choice of airflow creator

- Solution 1

- Advantages
- Disadvantage

- Solution 2

- Advantages
- Disadvantages

Solution 3

Advantages
Disadvantages

## TF3: Dry airflow Solution 1 :

## Choice of airflow creator

- Solution 1

- Advantages
- Disadvantage

- Solution 2

- Advantages
- Disadvantages

Solution 3

Advantages
Disadvantages

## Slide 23

PF1: Dry dietary products
Modular representation

Humid products

Prepare product
Trays
Pique
In a jumble

Exterior action

PF1: Dry dietary product

TF5: Create interaction between dry airflow and humid products
Shell
Vertical
Spread
Tunnel
Cylinder

Warm airflow

TF2: Create an airflow
Natural Convection
Forced Convection

TF3: Dry airflow
Air exchange
Absorption
Condensation

Dry and cold airflow

Warm airflow pulsed

Humid airflow pulsed

Dry products

Energy

Get product out

Dry products to pack

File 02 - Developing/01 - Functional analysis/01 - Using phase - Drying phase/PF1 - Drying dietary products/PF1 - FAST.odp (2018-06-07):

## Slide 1

How ?

Why ?

: And

: Inclusive Or (one or more possibility)

Principal function : Dry dietary product

: Exclusive Or (only one possibility)

Initial function

PF1 : Dry dietary product

Component functions

TF1: Increase flow temperature

Components

Solutions

Pompe à chaleur

Heat module 1

Solar thermal collector

Drying by temperature elevation

Usable flow

By solar input

Heat module 3

Resistor

By electrical input

By warm airflow

(Wood combustion, oil combustion, biomass)

Unusable flow

Oil combustor

Heat module 2

Wood combustor

Compost

Thermal exchanger

Pollute pipe

TF2: Create an airflow

Natural convection

Warm in-draught

Convection module 1

Positioning heater under drying room

Hole in the upper sides

Wind in-draught

Forced convection

Convection module 3

Electrical ventilator

Convection module 4

Wind ventilator

TF3: Dry airflow

Without conservation of air

Open pipe

Deshumidifier module 1

Air exchange

With conservation of air

Closed pipe

Deshumidifier module 2

Condensation

Deshumidifier module 3

Absorption

TF4: Link each module with airflow

Multi bloc

Pipe module 1

Linked organization

Mono bloc

Pipe module 2

All in drying

room

Compact organization

TF5: optimize interaction between dry airflow and humid products

Plenum

Freeze drying

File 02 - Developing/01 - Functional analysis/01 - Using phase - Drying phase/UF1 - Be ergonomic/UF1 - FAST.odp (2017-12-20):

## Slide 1

How ?

Why ?

: And

: Inclusive Or (one or more possibility)

Using Function : Be ergonomic

: Exclusive Or (only one possibility)

Initial function

UF1 : Be ergonomic

Component functions

Be adjustable

Components

Solutions

Be accessible to the user

Manual

Valve

Pipe interrupter

Automated valve

Contactor

Automate

Buttons

Automated

Not adjustable

No component

Let analyse of the product quality during the drying

Direct by the user

Be accessible to all part of the dryer

Size adapt to the user

Scale adapt to the user

By the user with sensor

Visual test

Camera

Screen

Hygrometric test

Weight sensor

Screen

Automatic

Automate

Weight sensor

H/M interface

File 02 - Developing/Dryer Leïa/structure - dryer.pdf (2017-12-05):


Insertion du fond par
l’intérieur pour éviter
que la structure gêne
les claies

Les coté des étagères
vissés à la structure en
bas et en haut et fixés sur le fond par des équerres

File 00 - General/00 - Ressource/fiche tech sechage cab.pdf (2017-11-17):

Rédigée par Sébastien BONDUAU (CAB) et Thibaut JOLIET (CFPPA de Montmorot) – juin 2013 Contact : 02-41-18-61-42 ou cab.filieres@biopaysdelaloire.fr

Réalisée avec le soutien financier du Conseil régional des Pays de la Loire et FranceAgriMer

# Dimensionnement

Le raisonnement est le suivant : « Je souhaite produire X kg de plante sèche à l’année, avec telle présentation et j’attends telle qualité de séchage. J’ai un pic d’activité sur tel mois de l’année où je dois sécher Y kg de plante par semaine, j’ai donc besoin de Y mètres carrés de claies.

- Je souhaite travailler avec un déshumidificateur, je choisi un appareil avec une capacité de déshumidification d’au moins Y litres/24h et une ventilation la plus importante possible, je dimensionne mon ventilateur par rapport à la ventilation de mon déshumidificateur en tenant compte des pertes de charges dans le circuit.
- Je souhaite travailler avec des capteurs solaires, j’ai besoin de Z = (Y/3) m² de capteur, je calcul ma ventilation pour arriver à une vitesse de circulation de l’air comprise entre 2 et 5 m/s (voir formule page précédente) en tenant compte des pertes de charge dans le circuit.
- Je souhaite travailler avec un système de chauffage de l’air ambiant, je compte 1kW de puissance pour 30 kg de

### capacité de chargement avec une ventilation comprise entre 200 et 500 m³ /h en tenant compte des pertes de

charge dans le circuit.

La plante; de l’eau diminue.

# Stockage

Les conditions de stockage de la plante une fois séchée doivent garantir sa conservation. Il doit donc se faire à l’abri de la lumière, des rongeurs, des insectes et dans des conditions hygrométriques favorables afin d’éviter toute reprise d’humidité (humidité relative inférieur à 50 %).

### Plusieurs solutions sont envisageables :

La désinsectisation peut se faire par congélation de le plante sèche pendant 48 h. Dans le cas de structures plus importantes avec système de commercialisation en gros, les conditions de stockage doivent être raisonnées en fonction des débouchés et des prix de vente. Les sacs tissés et les sacs« big-bag » ne garantissent pas des conditions de conservation optimum.

La solution la plus pertinente serait donc le stockage de ceux-ci dans un local dédié avec déshumidificateur. Cependant l’investissement dans ce local et les coûts de fonctionnement viennent accroître les coûts de production et diminuer d’autant la marge. Une étude économique incluant le facteur stockage est donc nécessaire.

Solution | Avantage | Inconvénient
Sacs kraft dans sacs plastique fermés ou cartons filmés. | Coût | Consommation importante
Sacs kraft rangés dans des fûts étanches (métal avec peinture alimen-taire ou plastique, les fûts cartons ne protègent pas la plante des re-prises d’humidité) | Coût | Difficultés de rangement (plusieurs plantes dans un même fût)
Sacs kraft ou cartons dans une pièce fermée et étanche avec déshumi-dificateur pour maintenir une humidité relative inférieur à 50 % | Pratique | Coût (investissement et fonc-tionnement)

Rédigée par Sébastien BONDUAU (CAB) et Thibaut JOLIET (CFPPA de Montmorot) – juin 2013 Contact : 02-41-18-61-42 ou cab.filieres@biopaysdelaloire.fr

Réalisée avec le soutien financier; La durée de séchage; (ventilation). • Elle ne devrait pas dépasser 5 jours.

du Conseil régional des Pays de la Loire et FranceAgriMer

# Principes

## Définitions :

Extraction de l’eau contenue dans la plante (l’air se charge de cette même quantité d’eau)

## Objectifs :

- Conservation de la plante (taux d’humidité de la plante autour de 12 %), de ses principes actifs et de sa couleur. Une plante sèche ou en cours de séchage peut reprendre l’humidité = moisissures, décoloration …Attention aux conditions de stockage et au reprise d’humidité lors du séchage.
- Qualité visuelle, organoleptique et bactériologique conforme aux exigences de l’acheteur.
- Diminution du volume et du poids.

Variables : eau (air et plante), température et durée.

- L’humidité de la plante avant séchage varie de 70 % (sarriette) à 90 % (basilic).
- L’eau se trouve dans chaque cellule de la plante et doit donc migrer à sa surface pour s’évaporer.
- Il existe des forces superficielles qui retiennent l’eau dans la plante, elles sont très faibles lorsque l’eau est abondante, elles deviennent de plus en plus fortes au fur et à mesure que la disponibilité

# L’air

- Il est composé d’air sec et de vapeur d’eau.
- Il se caractérise par sa température (T°C) et son taux d’humidité relative (HR%).
- La capacité de l’air à se charger en eau augmente en même temps que l’on augmente sa température, un air à 20°C et 60% d’humidité relative contient 10,5 g/m3 de vapeur d’eau alors qu’un air à 35°C et 60% d’humidité relative contient 24 g/m3 de vapeur d’eau.
- Le taux d’humidité relative est le pourcentage de vapeur d’eau contenu dans un m³ d’air par rapport au maximum que ce même m³ peut contenir à la même température.
- L’humidité absolue est la quantité totale de vapeur contenue dans l’air elle peut s’exprimer en g/ m³

- Elle varie en fonction du taux d’humidité et de la présentation ou granulométrie du produit à sécher, de l’humidité relative et de la température de l’air, du volume d’air passant par les plantes
- Elle n’est pas compressible en dessous d’un certain seuil à moins de travailler à haute température (6 h à 12 h pour une fleur type mauve, 48 h pour une partie aérienne, non découpée, type menthe).

# introduction

Rédigée par Sébastien BONDUAU (CAB) et Thibaut JOLIET (CFPPA de Montmorot) – juin 2013 Contact : 02-41-18-61-42 ou cab.filieres@biopaysdelaloire.fr

Réalisée avec le soutien financier


du Conseil régional des Pays de la Loire et FranceAgriMer

# Principes de fonctionnements des séchoirs à claies

b

## Plenum :

La taille de celui-ci doit permettre une bonne
répartition de l’air pulsé, il est possible d’y
installer des chicanes
pour casser le flux d’air
et obtenir un séchage
uniforme.

## Claies :

Dimensionnement :
Compter 1 % de la surface cultivée en surface de claies
performance du système de chauffage/déshumidification et des caractéristique du ventilateur).
Ou déterminer par un calendrier de récolte le pic d’utilisation du séchoir et compter 1 m² de claie par kg de plante fraîche à charger, prévoir une marge de sécurité suffisante afin d’anticiper un possible développement du volume à traiter.
Pour choisir la surface des claies, le meilleur rapport maniabilité/temps de manutention semble être autour d’1 m² avec des dimensions de type : 0,8 x 1,20 m. Des claies/ caissons (rebord entre 10 et 20 cm), en augmentant la capacité de chargement par m permettent une bonne économie de temps de travail, mais la ventilation doit être dimensionné en conséquence ( entre 500 et 1000 m
Matériaux : la toile supportant les plantes devra être lavable, classée alimentaire tout en permettant un bon passage du flux d’air (moustiquaire inox, store à fromage …)

c

Système de chauffage (fuel,

gaz, bois, électrique) :
Pour fuel et bois, les fumées de combustion ne doivent pas rentrer en contact avec les plantes, échangeur obligatoire.
Compter 1 kW pour 30 kg de capacité de chargement.

e

## Ventilateur :


Déshumidificateur : Caler le débit du ventilateur sur celui du déshumidificateur en tenant compte des pertes de charges et donc de la pression nécessaire au maintien de ce débit. Capteur solaire : Le débit de ventilateur est à calculer en fonction des capteurs pour obtenir une vitesse de l’air comprise entre 2 et 5 m/s. La formule est : débit en m3/h = vitesse de l'air en m/s x épaisseur de la lame d’air en m x largeur du capteur en m x 3600).
Tenir compte des pertes de charges et donc de la pression nécessaire.
Chauffage : compter 200 et 500 m3/h pour 30 kg de capacité de chargement en tenant compte des pertes de charge dans le circuit.

f


c

## Evacuation air humide :

Attention à éviter tout risque de condensation sur des parois froides.
Pour les systèmes avec capteur solaire sans ventilateur (convection naturel), la longueur de la cheminée conditionne le débit et la vitesse de l’air.
Pour les systèmes avec déshumidificateur (fonctionnement en circuit fermé avec recyclage de l’air), il est possible de placer le déshumidificateur dans l’enceinte de séchage afin de diminuer le coût de l’installation mais avec un temps de séchage allongé (déficit de ventilation).
Dans tous les cas si un gainage est nécessaire, attention aux pertes de charge, plus le section de gaine est importante moins il y a de perte de charge, attention aussi à ce qu’il y ait le moins possible de frein à une bonne circulation de l’air (coude, T …)

a

c

a

NB : Il est possible de coupler plusieurs systèmes, notamment pour un séchoir à capteur solaire dans une zone où l’ensoleillement
ou partiellement deux circuits d’air, un circuit fermé pour le déshumidificateur et un autre avec une entrée air ambiant réchauff
hygrostat. Dans le cas d’un couplage solaire/réchauffeur autre (électrique/bois …), seule l’arrivée d’air sera double, le système pourra être géré automatiquement à condition que la source alternative au solaire le soit aussi (chaudière à granulés, brûl fuel ou gaz, résistance électrique…).

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

Réalisée avec le soutien financier du Conseil régional des Pays de la Loire et FranceAgriMer

# Principes de fonctionnements des séchoirs à claies

## Claies :

Dimensionnement :
Compter 1 % de la surface cultivée en surface de claies (à moduler en fonction de la performance du système de chauffage/déshumidification et des caractéristique du ventilateur).
Ou déterminer par un calendrier de récolte le pic d’utilisation du séchoir et compter 1 m² de claie par kg de plante fraîche à charger, prévoir une marge de sécurité suffisante afin d’anticiper un possible développement du volume à traiter.
Pour choisir la surface des claies, le meilleur rapport maniabilité/temps de manutention semble être autour d’1 m² avec des dimensions de type : 0,8 x 1,20 m. Des claies/ caissons (rebord entre 10 et 20 cm), en augmentant la capacité de chargement par m² , permettent une bonne économie de temps de travail, mais la ventilation doit être dimensionné en conséquence ( entre 500 et 1000 m³ /h par m² de plancher)
Matériaux : la toile supportant les plantes devra être lavable, classée alimentaire tout en permettant un bon passage du flux d’air (moustiquaire inox, store à fromage …)

## Déshumidificateur :

Le choix du déshumidificateur est à faire en fonction du poids de plante à traiter, de la capacité d’investissement et de la vitesse de séchage voulue.

La capacité de déshumidification pour un séchage de durée moyenne devra être d’environ 1 litre/24h pour 1 m² de claie.

Si l’on souhaite accélérer le séchage il est possible de partir sur une capacité supérieure, attention au risque de surchauffe.

d

## Ventilateur :

Déshumidificateur : Caler le débit du ventilateur sur celui du déshumidificateur en tenant compte des pertes de charges et donc de la pression nécessaire au maintien de ce débit. Capteur solaire : Le débit de ventilateur est à calculer en fonction des capteurs pour obtenir une vitesse de l’air comprise entre 2 et 5 m/s. La formule est : débit en m3/h = vitesse de l'air en m/s x épaisseur de la lame d’air en m x largeur du capteur en m x 3600).
Tenir compte des pertes de charges et donc de la pression nécessaire.
Chauffage : compter 200 et 500 m3/h pour 30 kg de capacité de chargement en tenant compte des pertes de charge dans le circuit.

c

## Capteur solaire thermique air :

La surface de capteurs est à calculer en fonction des besoins en énergie du système. Compter 1 m² de capteurs pour 3 à 5 m² de claies.
Les capteurs ayant les meilleurs rendements sont ceux ayant deux lames d’air : une lame d’air statique (entre le vitrage et le corps noir) et une lame d’air dynamique (entre corps noir et fond de caisson)

g

a

Et aussi ...

## Temps de travail :

Le temps de chargement et déchargement est directement conditionné par la taille des claies et par l’agencement espace de travail - espace de séchage. L’espace de travail doit être raisonné pour minimiser les déplacements et la manutention, il doit comporter une table de travail, un espace de rangement des claies, un espace de rangement pour les sacs, les tamis, balance…. Il doit être en conformité avec la réglementation.

## Investissement :

L’investissement est directement lié au dimensionnement du système (comme pour la rationalisation des coûts de fonctionnement, l’investissement dans un système de séchage doit se faire au plus près des besoins de l’exploitation avec une marge de manœuvre nécessaire correspondant au développement de celle-ci).
Un système de production (1 UTH) avec valorisation des plantes produites par la transformation n’a, à priori, pas intérêt à investir plus de 1000 € à 1500 € dans son système de séchage (laissant ainsi de la capacité de financement pour le matériel de production et de transformation, c’est à relativiser en fonction de la taille de l’atelier plantes à tisanes commercialisées en l’état).
A contrario, un système de production plus important visant en vitesse de croisière une production annuelle supérieure à 100 kg (valorisée en vente directe ou non) devra se diriger vers des systèmes plus performants et donc plus onéreux.

## Coût de fonctionnement :

Il est primordial de maîtriser sa consommation d’énergie d’une part pour limiter les coûts de fonctionnement et donc les charges et d’autre part pour limiter l’impact écologique de l’activité. Pour ce faire :
- Dimensionner l’installation au plus proche de vos besoins en anticipant tout de même une évolution du système qui puisse se faire en parallèle du développement de l’activité.
- Rationaliser l’utilisation du système = gestion rigoureuse du fonctionnement. = remplissage maximum sur une durée minimum

n’est pas suffisant. Dans le cas d’un couplage solaire/déshumidification, il faudra nécessairement différencier, totalement auffé et une sortie d’air humide, le passage d’un circuit à l’autre peut être géré automatiquement par un binmme thermostat/ tème pourra être géré automatiquement à condition que la source alternative au solaire le soit aussi (chaudière à granulés, brûleur

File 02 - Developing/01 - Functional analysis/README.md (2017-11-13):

# Functional analysis

## Vocabulary
- The need: is the goal of a product
- Function: a function is an action, a service or a constraint of a product
- Interactor: all element which have a contact or a relation with the product
- Phase: different using phase (using phase, supplying phase, cleaning phase …)

## The aim
The functional analysis is a design method which divise the need of a product, or a service, in different functions to create a group of very simple studies.

## The process
The process is decompose in different analysis :
**- Phase analysis:** the phase correspond to the different kind of using of the product, like using phase, supplying phase, cleaning phase ... In that part of the study, we list all of the phase. For each phase, different function can appeared and exist only for that phase.

For our study, we try to explore the most of solution at the beginning, to after, if we want, reduce the study to a few of function which interess us. The aim of that practice is to open a maximum of solutions, and motivate people to realise complementary studies.

**- Octopus diagram**: representation of the product, the study, and the interactor, all ellement in relation with the product. Each interaction, will be defined by a function of the product :
- PF: principaly function, that's the need of the product
- UF: using fonction, that's the condition to have a good using of the product
- CF: constraint function, that's the limit of the using



>Octopus diagram

**- Interactors characterisation:** now, we difined all interactors of the product, we describe the interactor, with important characteristic which influence study. In our practice, we try to make a modular and scaling model, the that part of the study, need to identified different group in each interactors which create a different product, write about that to let other group, peoples or we, later, develop complementary products.

**- Functions characterisation:** like with the interactor, we write important characteristic which influence study.

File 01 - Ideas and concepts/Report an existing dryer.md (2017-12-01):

# How to report an existing dryer 
 
*Inspired from “Méthodologie TRIP” by l’Atelier Paysan*

We try to summarise information about dryers, so to the technical approach, the 1st thing to do is to report lot of different kinds of existing dryers.

On that document we try to explain how have enough informations for the report.
That way isn’t the only way to have enough information, the more important is the 3rd part, semi-structured interview.
We try to make it for industrial products and DIY products so, maybe the is some answer specific for each category.

## I) Know different kinds of dryer
To present a dryer is be good to know what kind of dryer already existing, for that you can go on internet or on our [state of art](https://github.com/Gillou38/Drying-open-source-solution/blob/master/01%20-%20Ideas%20and%20concepts/State%20of%20art.md), we try to make a good data base about dryers, and using technologies.

## II) Useful materials
- camera
- tape measure
- audio recorder
- takes notes and drawings

## III) Semi-structured interview
First, ask if you can record the interview if you want to do it.

### Principle
- Generic name link with using
- What the aim (drying fruits, plants, all kind of product...)
- That’s a DIY dryer?
######	- Why make it? (cheaper, custom product, pleasure, more simple)
######	- There is preliminary state before the fabrication (inspirations, drawings, plans…)
######	- What’s the development? (success, failure, questioning …)

### Making (for DIY)
- What’s the materials? (mechanical, electrical, new materials, raw material dump)
- tools and technique
- construction site’s organisation (time and space)
- price (approximate)
 
### Making (for industrial products)
- Constructor, reference …

### Using
- Technical characteristic
- Global size, between each components
	- kind of deshumidifer
	- heating system
	- convection system
	- ...
- How components work together (components organisation)
- Using process
	- Preparation
	- Using
	- End
- Danger

### Using feedback (for DIY)
- Evolution between the construction and now
- Difference between first idea and the using
- What could they do differently?
- Maintenance/using cost

### Using feedback (for industrial products)
- Difference between need and the using
- Maintenance/using cost

### Illustration
- Photo will be a good method to show the product
- Diagram for “how product works”
- photo during fabrication

### Contact
If we want to contact again the user, and if he’s agree.

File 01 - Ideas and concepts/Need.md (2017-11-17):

# The need

## Who’s the users:
Food producer (solid food, not liquid food)

## What kind of product: solid products, centimeter scale
- Vegetables, moist food
- Aromatics and medicinal plants
- Cheese
- Nuts
- Cereal

## What’s the aim: 
Dry food with airflow

## Causes: 
- improve food conservation
- create new products

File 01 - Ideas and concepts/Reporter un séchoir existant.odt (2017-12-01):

TRIP (pour séchoir)

I) recherche des auto-constructeurs

A) diffuser appel

- équipe de l’AP

- contact perso

- réseaux agri bio et paysanne (p11)

B) Présentation

- mail de prez pour réseaux (p9-10)

II) Contact auto-constructeur

a) préz structure et démarche

b) info sur les réalisation

- quelle utilisation du produits (pro/amateur, bouffe/autre)

- connaissance nécessaire (méca, élec, autom)

- brevetage

- fonctionnelle/en dev

- niveau de complexité

- niveau d’auto construction (complète, modif d’un séchoir existant)

III) Préparer entretien

a) État de l’art

b) Matos

- appareil photo

- mètre

- enregistreur audio

- note, croquis …

IV) Sur place

a) Entretien semi directif

Toutes les informations sont intéressantes d’un point de vue personnel, mais toutes ne sont pas forcément pertinentes dans le cadre des restitutions

L’objectif principal étant bien évidemment la réalisation, son sens, sa construction, et son usage.

Il est donc toujours utile de collecter beaucoup d’informations mais, plus on en a, plus il faut s’apprêter à trier tout ceci par la suite.

- enregistrement avec permission

- prez rapide et général de l’exploit

- détail de la machine devant elle

(- dernier tour sans le producteur, avec autorisation)

b) Les thèmes à aborder

Il n’aurait aucun sens de se contenter de poser ces questions les unes après les autres.

CONTEXTE

- type de production

- volume de prod

- contexte climatique

- grande ligne du parcours depuis l’instal

- évolution de l’ambition

- maint d’œuvre et orga du travail

- mode de commercialisation

RÉALISATION

Principe

- Nom générique en lien avec l’usage

- A quoi ça sert

- Auto construction ?

- Pourquoi le faire soi même (moins cher, sur mesure, plaisir, plus simple)

- étape préliminaire à l’auto construction (inspirations, croquis, plan …)

- Cheminement (réussites, échecs, remise en question)

Construction

- matériaux (méca, élec, neuf, récup)

- techniques et outils

- organisation du chantier (temps et espace)

- coût (approximatif)

Usage

- caractéristique technique

- mesure totale, entre chaque élément

- déshu

- chauffe

- convection

- fonctionnement des composants ensemble

- process d’utilisation (s’il y a quelque chose de particulier)

- préparation

- en utilisation

- fin

- Risques

Retours sur l’utilisation

- Évolutions entre la construction et maintenant

- différences entre l’idée de base et la pratique

- si c’était à refaire ?

- Coût d’entretien/utilisation

C) Illustrations

- beaucoup de photo

- faire des schémas (ensemble, détails)

- photo pendant la fab

D) Pour publi sur le forum de l’AP avec authorisation

Carte des auto-constructeurs : http://tinyurl.com/goqfkbn

- Info nécessaire :

- adresse

- lien vers le forum

- nom et prénom

- Optionnel :

- nom de la structure

- tel

- mail

D) Relire les notes le soir

V) Poster sur le forum

P25

Inspiré de la méthodologie TRIP de l’atelier paysan

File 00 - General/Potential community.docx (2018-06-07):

# Potential community

Other people or community who can be interest to work with us.

Forum:

- L’atelier paysan : https://forum.latelierpaysan.org/participative.html
- Permies : https://permies.com/forums
- OSHWA – open hardware forum : http://community.oshwa.org/
- OSE : http://forum.opensourceecology.org/categories/partnerships
- Makershare : https://makershare.com/projects
- Open source: https://www.open-source-forum.com/forum
- Libre : https://forum.framasoft.org/viewforum.php?f=12&sid=4dd5d2012c6967997d28eabdeefdabb6
- https://plus.google.com/communities/105413589856236995389

Company which made kit of solar dryer:

- http://www.kitsechoirsolaire.com/

Company which use other technology of drying:

- http://www.abcar-dic.com/fr/applications-technologiques#swell-drying

Labo séchage :

- Cirad : https://plateforme-technologie-agroalimentaire.cirad.fr/plateaux-techniques/deshydratation
- Labo Maghrebin : https://www.smsts2018.com/
- Auri : http://www.auri.org

Labo PPAM :

- http://www.iteipmai.fr/

Maker:

- http://www.instructables.com/id/Solar-Food-Dryer/
- http://velacreations.com/howto/solar-food-dryer/
- http://www.appropedia.org/Chris%27s_ENGR305_Solar_Food_Dehydrator

Forum ingénieur mécanique :

- http://www.eng-tips.com/threadminder.cfm?pid=281
- http://cr4.globalspec.com/section/mechanical-engineering
- https://www.physicsforums.com/forums/open-practice-problems.250/
- https://www.engineersedge.com/engineering-forum/forumdisplay.php/52-Mechanical-Engineering-Forum
- https://www.engineeringclicks.com/forum/forums/mechanical-design-news-events.43/

Inspiration:

- https://permies.com/t/40/3562/kitchen/Solar-Food-Dryers


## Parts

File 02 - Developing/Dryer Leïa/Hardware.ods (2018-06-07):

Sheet: Materials
 | Components | Kind | Description | Materials | Production | Advantage | Disadvantage | Thickness (or sizing description) | Reseller | Selling by | Price | Link
Trays | Screen/Fabric | Ripening mat |  | Food grade polypropylene |  | Alimentaire, Cheap |  |  |  | Alliance elevage |  | https://www.alliance-elevage.com/dept80_80_02_011_0800538_fiche_store_1m_maille_5x5mm_ml_5216.html
 |  | Aging racks |  | Stainless |  | Alimentaire | Expensive
 |  | Mosquito net |  | Aluminium
 |  |  |  | Plastique (foodgrade ?)
 |  |  |  | Nylon
 |  |  |  | Stainless
 |  | Hessian for cheese |  | Flax (lin)
 |  | Hessian for butter |  | Cotton
 | Trays batten | Batten | Plane | Pin |  | Very cheap | Plane it
 |  |  | Non-plane | Pin |  | Don't need tools | Expensive
 |  | Board | Plane | Pin
 |  |  | Non plane | Pin
Structure | Panel | OSB |  | Resin less particule | Industrial | Easy to assembly, Good airtightness, Cheap, Free-standing |  | 12 mm | Matériaux naturels | Slab 90x205 cm | 7 €/m² | http://www.materiaux-naturels.fr/fiche-875/panneau-osb-3-sans-formaldehyde-ajoute.html
 |  |  |  | Resin less particule | Industrial |  |  | 12 mm | Alpes éco matériaux | Slab 125x250 cm | 6,93 €/m² | http://alpes-ecomateriaux.com/bois/62-panneaux-osb3.html
 |  | Parquet floor Raw timber (bois brut) |  | Pin | Local |  |  |  |  |  | ~28€
 |  | 3pli panel |  |  | Industrial | Free-standing, Easy to assembly, Good airtightness |  |  |  |  |  | http://www.ravier.fr/panneaux-bois-massifs-3pli-tripli-jura-france-panneau-3plis-massif.html
 | Structure batten | Board
 |  | Batten
 | Gaine |  |  |  |  |  |  |  |  |  |  | https://www.amazon.fr/Gaine-aluminium-extracteur-winflex-ventilation/dp/B0184BW1L2

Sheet: Electrical
 | Components | Kind | Brand | Ref. | Size | Flow capacity | Electrical power | AC/DC – Intensity | Air direction | Unit price | Conditionning | Total price | Description | Link
Power | Ventilator | Propeller (hélice) |  |  |  |  |  | 12 V DC |  |  |  |  | 100 m^3/h | https://www.cdiscount.com/bricolage/quincaillerie/ventilateur-12v-100m3-h/f-1660319-sel3758941965106.html
 |  |  |  |  |  |  |  |  |  |  |  | 24,00 € | 300m^3/h | http://www.lorvert-paris.com/growshop-hydroponique-culture-indoor/ventilation-extracteur-air/extracteur-air-axial-S-P/extracteur-air-axial-gaine-dospel/1070.h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
 |  |  |  |  |  |  |  |  |  |  |  |  | 305 m^3/h | https://www.amazon.fr/VENTS-Extracteur-gaine-150mm-Vents/dp/B005GK3WVI
 |  | Centrifugal | Torin | SV10-10-900 | 424 x 379 x 331 mm | 3250 m^3/h | 550 W |  | Perpendicular |  |  |  | Class IP 44, Tmax = 50°C | http://reseau-ventilation.oxygen-industry.com/index.php/extracteur-torin-sv10-10-900-debit-3250-m3-h.html
 |  |  |  |  | Ø 430 | 1800m^3/h | 318 W | 230V – 50 Hz – 1,39 A | Linear |  |  | 249,00 € | classe IP44, Tmax = 40°C | http://reseau-ventilation.oxygen-industry.com/index.php/extracteur-air-centrifuge-systemair-rvk-315e2-l1-diam-315-mm-debit-1800-m3-h.html
 |  |  |  |  | Ø 315 mm | 1700m^3/h | 225 W |  | Linear |  |  | 219,00 € | classe IP44 | http://www.lorvert-paris.com/growshop-hydroponique-culture-indoor/ventilation-extracteur-air/extracteur-air-centrifuge-rvk-bk/extracteur-air-centrifuge-s-vent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
 |  |  | RVK UFO |  | Ø200 mm | 1000 m^3/h |  |  | Linear |  |  | 159,00 € | classe IP 44, faible niveau sonore | http://www.lorvert-paris.com/growshop-hydroponique-culture-indoor/ventilation-extracteur-air/extracteur-air-centrifuge-rvk-bk/extracteur-air-centrifuge-system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
 |  | Turbine
 |  | Wind forced
 | Components | Kind | Brand | Ref. | Size | Dehu capacity | Electrical power | AC/DC – Intensity
 | Dehumidifier | Condensation | Trotec | TTK 350 S | 575 x 520 x 965 mm | 70 L/jour |  | 230 V Dc – 5,8 A |  | 504,16 € | 1 | 504,16 | 1000 m^3/h ; promotion price
 |  |  | Alpatec
 |  |  | Pur line
 |  |  | Rexair
 |  |  | CFT
 |  | Absorption
 |  |  |  |  |  |  |  |  |  |  |  |  | 12 – 36 V ; 10 A ; Pmax = 200 w | http://tiptopboards.com/282-controleur-de-moteur-%C3%A0-courant-continu-12v-36v-10a-.html
 | Heater
 | Heat exchanger
Automation | Rotation variator |  |  |  |  |  |  | 12 – 36V
 |  |  |  |  |  |  | 300W | 220V |  |  |  |  |  | https://www.amazon.fr/Chacon-54042-Prise-variateur-Blanc/dp/B0033ZP2IO
 | Temperature regulator |  |  |  |  |  |  | 230 V Dc |  | 50,00 € | 1 | 50 | -40 to + 90 °C ; Contactor : 230V, 2A | http://www.conrad.fr/ce/fr/product/198545/Rgulateur-de-temprature-1004-D-40-90-C-Relais-2-A-1-pcs;jsessionid=A431ED687B0272003DE3E313C556E460.ASTPCEN19
 |  |  |  |  |  |  |  |  |  |  |  |  | -60 to + 150 °C ; Contactor : 230V, 8A | http://www.conrad.fr/ce/fr/product/197498/Rgulateur-de-temprature-Enda-ET1411-NTC-230-NTC-60-150-C-Relais-8-A-1-pcs
 | Sonde température |  |  |  |  |  |  |  |  |  |  |  |  | https://www.amazon.fr/Plug-n-Play-Contr%C3%B4leur-Temp%C3%A9rature-Refroidissement-Fermentation/dp/B016EYB03G (https://www.amazon.fr/Plug-n-Play-Contrôleur-Température-Refroidissement-Fermentation/dp/B016EYB03G)

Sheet: Fix
 | Components | Size | Material | Unit price | Conditionning | Total price | Supplier | Description | Link
Fix | Square | 40x40 mm | Zinc plated steel | 0,78 | 12 | 9,35 | Leroy Merlin |  | https://www.leroymerlin.fr/v3/p/produits/12-equerres-d-angle-40-x-40-mm-e22359
 |  | 30x30 mm | Zinc plated steel | 0,5 | 1 | 0,5 | Leroy Merlin |  | https://www.leroymerlin.fr/v3/p/produits/equerre-d-assemblage-magnodur-l-30-x-l-30-mm-e1400146333
 |  | 50x40 mm | Zinc plated steel | 0,91 | 12 | 10,9 | Leroy Merlin |  | https://www.leroymerlin.fr/v3/p/produits/12-equerres-d-angle-50-x-40-mm-e22358
 | Side panel joint | 240 x 80 mm | Zinc plated steel | 3,5 | 1 | 3,5 | Leroy Merlin |  | https://www.leroymerlin.fr/v3/p/produits/patte-d-assemblage-240-x-80-mm-e1400146229
 |  | 140 x 55 mm | Zinc plated steel | 1,8 | 1 | 1,8 | Leroy Merlin
 |  | 40 x 160 | Zinc plated steel | 1,4 | 1 | 1,4 | Leroy Merlin |  | https://www.leroymerlin.fr/v3/p/produits/patte-d-assemblage-160-x-40-mm-e1400146200
 |  | 80 x 40 | Steel | 0,8 | 1 | 0,8 | Leroy Merlin |  | https://www.leroymerlin.fr/v3/p/produits/patte-d-assemblage-magnodur-l-80-x-l-40-mm-e1400146325
 | Hinge | 100 x 30 mm | Steel | 1 | 1 | 1 | Leroy Merlin |  | https://www.leroymerlin.fr/v3/p/produits/charniere-de-table-magnodur-l-100-x-l-30-mm-e1400146303
 | Flat square | 200 x 30 mm | Zinc plated steel | 3,1 | 1 | 3,1 | Leroy Merlin |  | https://www.leroymerlin.fr/v3/p/produits/equerre-fenetre-200-x-30-mm-e1400146213
 |  | 75 x 30 mm | Zinc plated steel | 0,8 | 1 | 0,8 | Leroy Merlin |  | https://www.leroymerlin.fr/v3/p/produits/equerre-fenetre-75-x-30-mm-e1400146208
 | Adjustable square | 25 x 30 | Zinc plated steel | 0,6 | 1 | 0,6 |  | For panel/panel fixation | https://www.leroymerlin.fr/v3/p/produits/equerre-ajustable-ajustable-30-x-25-mm-e1400146202

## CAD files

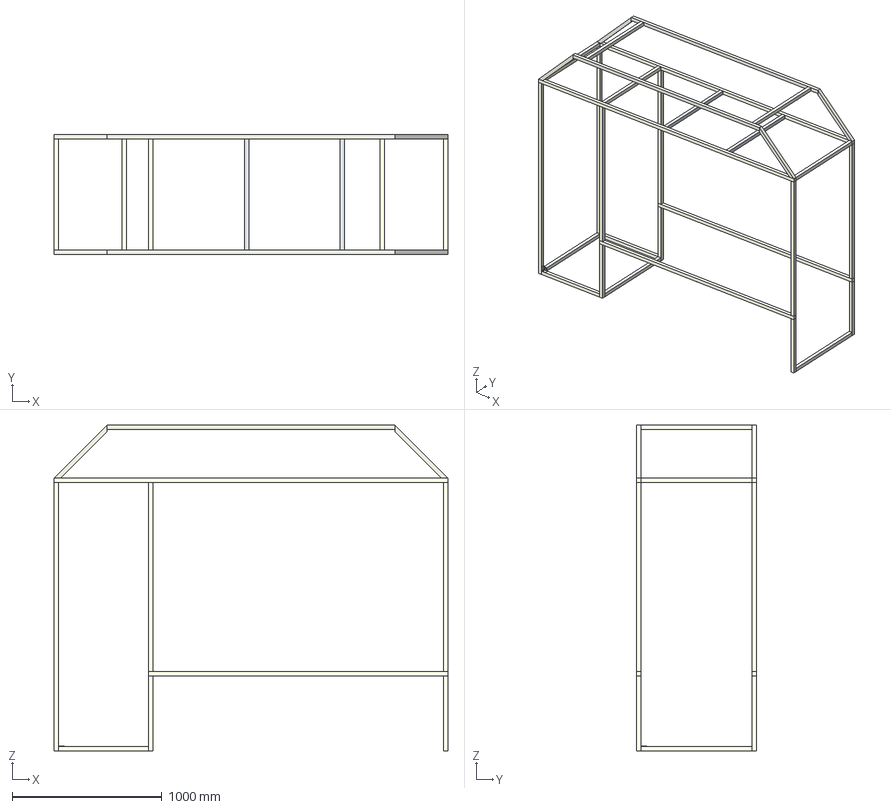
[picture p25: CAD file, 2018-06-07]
02 - Developing/Dryer Leïa/CAD/Dryer_Leïa_complete.FCStd
2630.0 x 800.0 x 2173.6 mm
FR_beam_1
TB_long_beam_F
TB_long_beam_R
FR_beam_2
LR_long_beam_F
LR_long_beam_R
LR_beam_side_room_F
LR_beam_side_room_R
FR_beam_3
TB_bottom_room_beam_FL
TB_bottom_room_beam_RL
TB_bottom_room_beam_FR
TB_bottom_room_beam_RR
FR_beam_4
FR_beam_5
TB_top_room_beam_FL
LR_bottom_room_beam_F
LR_bottom_room_beam_R
TB_top_room_beam_RL
TB_top_room_beam_FR
TB_top_room_beam_RR
Top_room_beam_high_left
Top_room_beam_high
FR_upper_room_beam
RR_upper_room_beam
FL_upper_room_beam
RL_upper_room_beam
F_upper_room_long_beam
R_upper_room_long_beam
L_upper_room_beam
R_upper_room_beam
Clone of L_structure_beam_size_with_both_sides_holes
Clone of Clone of L_structure_beam_size_with_both_sides_holes
Clone of Clone of Clone of L_structure_beam_size_with_both_sides_holes

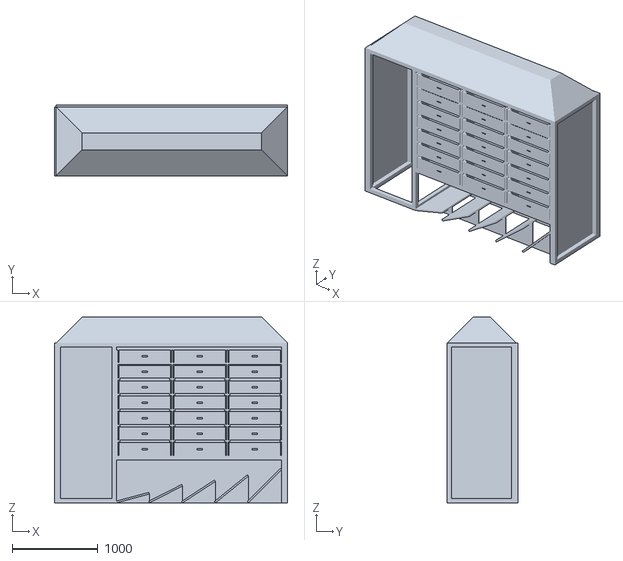
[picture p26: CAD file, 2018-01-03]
02 - Developing/Dryer Leïa/CAD/STL exports/Full assembly.stl
2710.0 x 820.0 x 2160.0

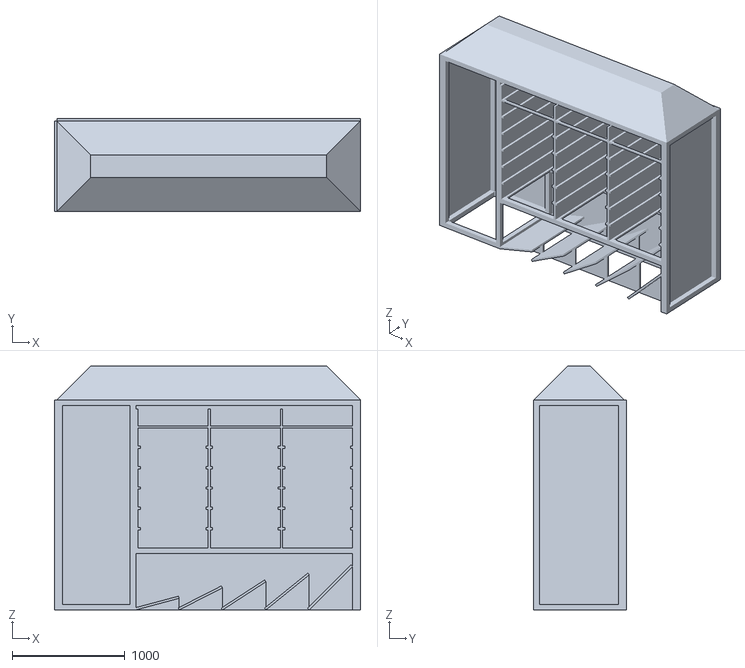
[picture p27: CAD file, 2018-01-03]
02 - Developing/Dryer Leïa/CAD/STL exports/Structure.stl
2710.0 x 820.0 x 2160.0

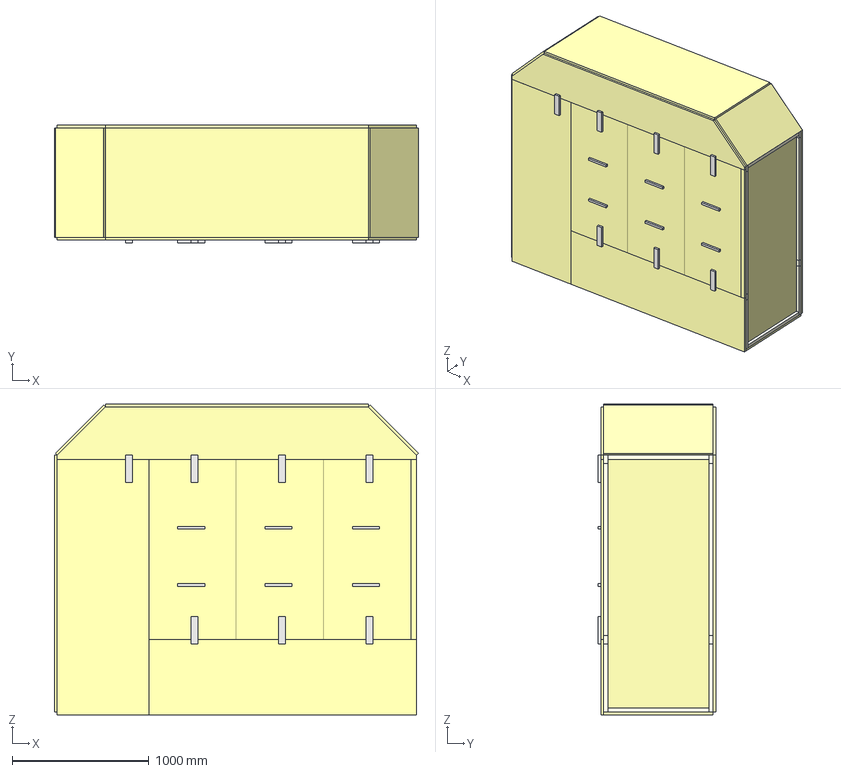
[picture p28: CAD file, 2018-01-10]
02 - Developing/Dryer Leïa/CAD/Dryer_Leïa_renforced.FCStd
2664.1 x 860.0 x 2273.6 mm
FR_beam_1
TB_long_beam_F
TB_long_beam_R
FR_beam_2
LR_long_beam_F
LR_long_beam_R
LR_beam_side_room_F
LR_beam_side_room_R
FR_beam_3
TB_bottom_room_beam_FL
TB_bottom_room_beam_RL
TB_bottom_room_beam_FR
TB_bottom_room_beam_RR
FR_beam_4
FR_beam_5
TB_top_room_beam_FL
LR_bottom_room_beam_F
LR_bottom_room_beam_R
TB_top_room_beam_RL
TB_top_room_beam_FR
TB_top_room_beam_RR
Top_room_beam_high
FR_upper_room_beam
RR_upper_room_beam
FL_upper_room_beam
RL_upper_room_beam
F_upper_room_long_beam
R_upper_room_long_beam
L_upper_room_beam
R_upper_room_beam
Rear_panel
Side_panel_left
Top_room_panel_left
Top_room_panels
Top_room_panel_R_unfinished
Side_room_floor
Upper_room_panel_L
Upper_room_panel_R
Upper_room_panel_T
Upper_room_panel_F
Bottom_room_panel
Little_front_panel
Top_room_panel_R
Drawer_array
Drawer_supports_L
Drawer_supports_R
Drawer_supports_lower_row_L
Drawer_supports_lower_row_R
Drawer_support_L
Drawer_support_R
Drawer_support_lower_row_R
LB_dehumidifier_beam
RB_dehumidifier_beam
FT_dehumidifier_beam
RT_dehumidifier_beam
Side_room_door
Top_room_doors
Locking_side_room
Locking_top_rooms
Handles_door_top_room

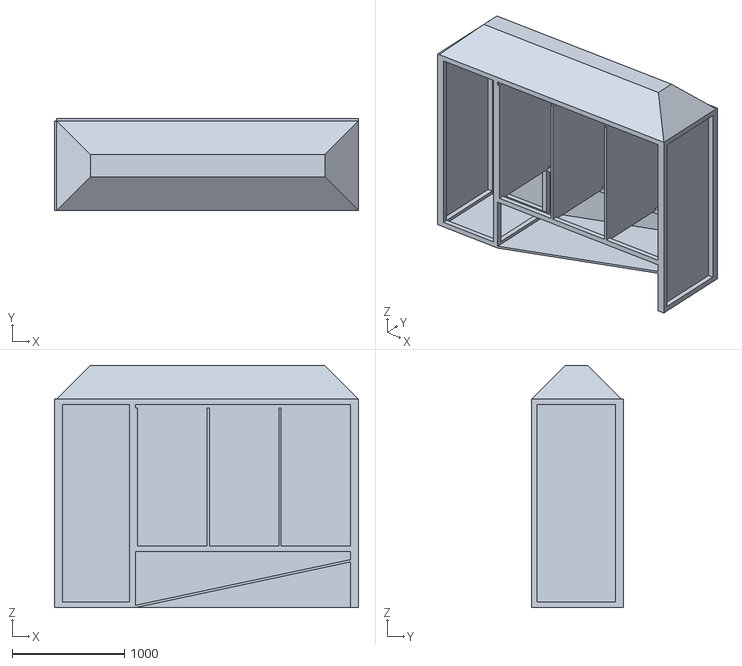
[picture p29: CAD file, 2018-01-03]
02 - Developing/Dryer Leïa/CAD/STL exports/Structure_alternativePlenum2.stl
2710.0 x 820.0 x 2160.0

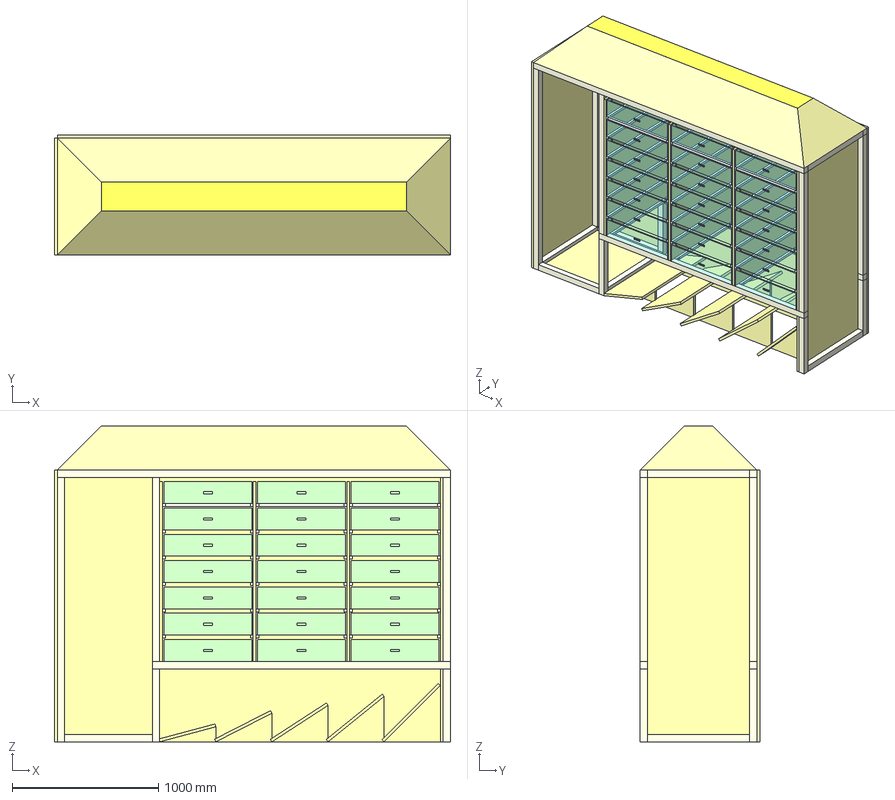
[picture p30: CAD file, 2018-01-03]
02 - Developing/Dryer Leïa/CAD/Dryer_Leïa.FCStd
2710.0 x 820.0 x 2160.0 mm
FR_beam_1
TB_long_beam_F
TB_long_beam_R
FR_beam_2
LR_long_beam_F
LR_long_beam_R
LR_beam_side_room_F
LR_beam_side_room_R
FR_beam_3
TB_bottom_room_beam_FL
TB_bottom_room_beam_RL
TB_bottom_room_beam_FR
TB_bottom_room_beam_RR
FR_beam_4
FR_beam_5
TB_top_room_beam_FL
LR_bottom_room_beam_F
LR_bottom_room_beam_R
TB_top_room_beam_RL
TB_top_room_beam_FR
TB_top_room_beam_RR
Rear_panel
Side_panel_left
Top_room_panel_left
Top_room_panels
Top_room_panel_R
Top_panel_45d_L
Top_panel_45d_Right
Top_panel_45d_F
Top_panel_45d_Rear
Top_panel
Side_room_floor
Drawer_array
L_drawer_beam_FBL
L_drawer_beams_FBL
L_drawer_beams_FBR
L_drawer_beam_FBR
L_drawer_beam_RBL
L_drawer_beams_RBL
L_drawer_beam_RBR
L_drawer_beams_RBR
L_drawer_beam_TRL
L_drawer_beams_TRL
L_drawer_beam_TRR
L_drawer_beams_TRR
Drawer_supports_L
Drawer_supports_R
Drawer_supports_lower_row_L
Drawer_supports_lower_row_R
Structure_top_room_LR_small_beams
Drawer_support_L
Drawer_support_R
Drawer_support_lower_row_R
Structure_top_room_LR_small_beam
Support_plenum_1_F
Support_plenum_1_R
Support_plenum_2_F
Support_plenum_2_R
Support_plenum_3_F
Support_plenum_3_R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

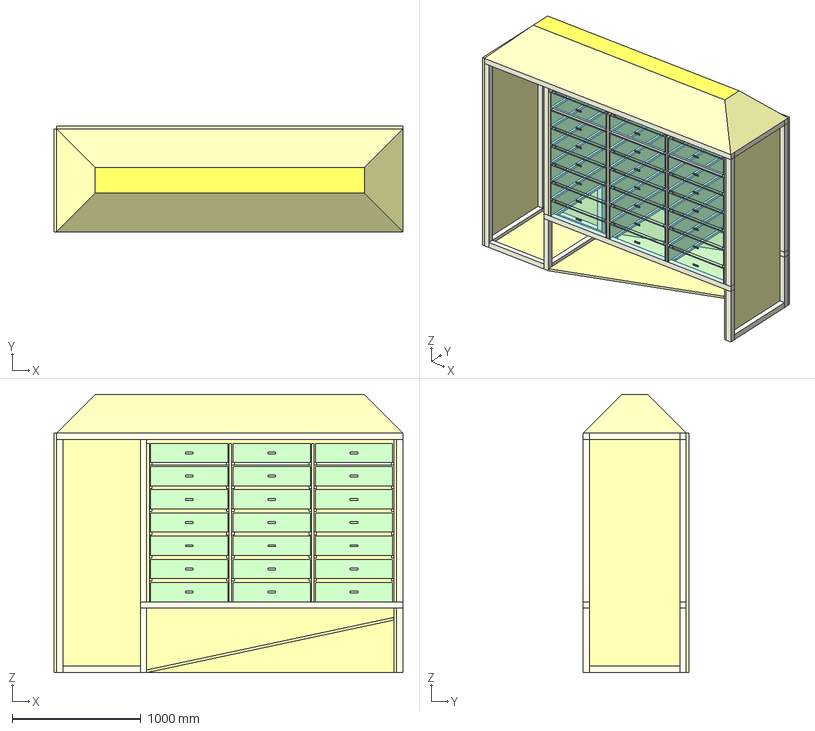
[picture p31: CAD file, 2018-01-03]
02 - Developing/Dryer Leïa/CAD/Dryer_Leïa_alternativePlenums2.FCStd
2710.0 x 820.0 x 2160.0 mm
FR_beam_1
TB_long_beam_F
TB_long_beam_R
FR_beam_2
LR_long_beam_F
LR_long_beam_R
LR_beam_side_room_F
LR_beam_side_room_R
FR_beam_3
TB_bottom_room_beam_FL
TB_bottom_room_beam_RL
TB_bottom_room_beam_FR
TB_bottom_room_beam_RR
FR_beam_4
FR_beam_5
TB_top_room_beam_FL
LR_bottom_room_beam_F
LR_bottom_room_beam_R
TB_top_room_beam_RL
TB_top_room_beam_FR
TB_top_room_beam_RR
Rear_panel
Side_panel_left
Top_room_panel_left
Top_room_panels
Top_room_panel_R
Top_panel_45d_L
Top_panel_45d_Right
Top_panel_45d_F
Top_panel_45d_Rear
Top_panel
Side_room_floor
Drawer_array
L_drawer_beam_FBL
L_drawer_beams_FBL
L_drawer_beams_FBR
L_drawer_beam_FBR
L_drawer_beam_RBL
L_drawer_beams_RBL
L_drawer_beam_RBR
L_drawer_beams_RBR
L_drawer_beam_TRL
L_drawer_beams_TRL
L_drawer_beam_TRR
L_drawer_beams_TRR
Drawer_supports_L
Drawer_supports_R
Drawer_supports_lower_row_L
Drawer_supports_lower_row_R
Structure_top_room_LR_small_beams
Drawer_support_L
Drawer_support_R
Drawer_support_lower_row_R
Structure_top_room_LR_small_beam
Plenums_serie

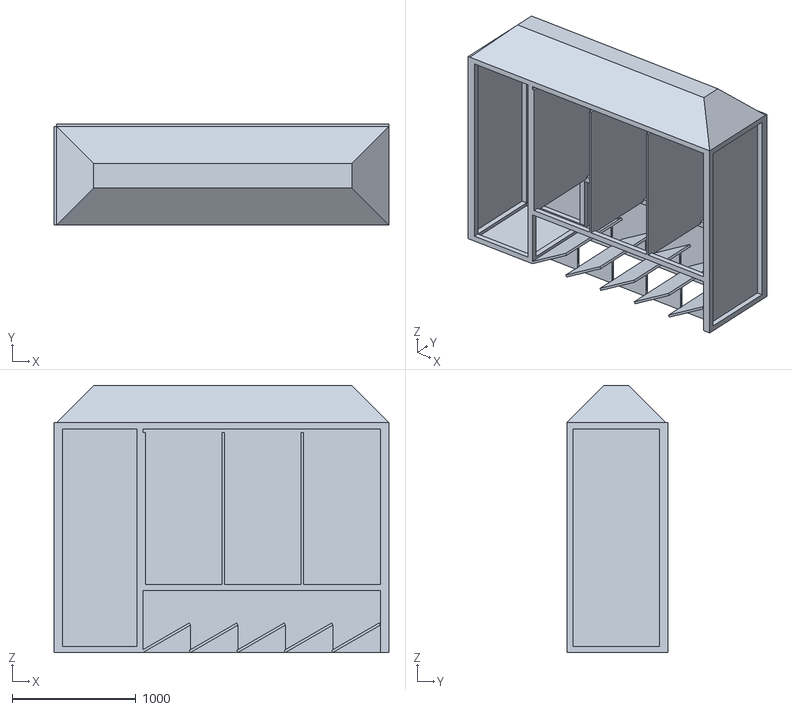
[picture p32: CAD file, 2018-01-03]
02 - Developing/Dryer Leïa/CAD/STL exports/Structure_alternativePlenum1.stl
2710.0 x 820.0 x 2160.0

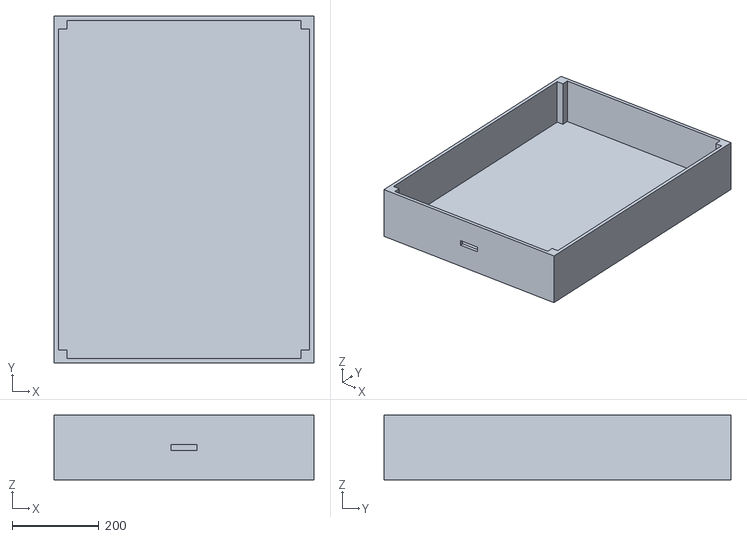
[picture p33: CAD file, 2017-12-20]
02 - Developing/Dryer Leïa/CAD/STL exports/Drawer.stl
600.0 x 800.0 x 150.0

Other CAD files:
02 - Developing/Dryer Leïa/CAD/Dryer_Leïa_alternativePlenums1.FCStd

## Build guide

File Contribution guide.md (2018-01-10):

Contribution guide
==================

This project is open to any interested person wanting to contribute, whatever
their motivations, may they be personal or professional, and whatever their
competences. The more we are, the better the dryer will be and the higher the
chances will be that it will be actually used.

Don’t hesitate to participate in one or more of the following activities:

1.  Promotion of the project (speak or report about the project, share links and
    so on)

2.  [Idea
    sourcing](https://github.com/Gillou38/Drying-open-source-solution/tree/master/01%20-%20Ideas%20and%20concepts)

    1.  [Propose ideas to
        develop](https://github.com/Gillou38/Drying-open-source-solution/issues)

    2.  Document existing designs

    3.  [Organised state of
        art](https://github.com/Gillou38/Drying-open-source-solution/blob/master/01%20-%20Ideas%20and%20concepts/State%20of%20art.md)

    4. Document drying science with engineer, scientific and farmer point of view

3.  [Development](https://github.com/Gillou38/Drying-open-source-solution/tree/master/02%20-%20Developing):
    [Formalisation of technical
    problems](https://github.com/Gillou38/Drying-open-source-solution/tree/master/02%20-%20Developing/01%20-%20Functional%20analysis)
    (Functional analysis)

    1.  Propose and develop technical solution (FAST - Function Analysis System
        Technique)

    2.  Organization of technical solution in the process (SADT - Structured
        Analysis and Design Technic)

    3.  Choice of technical solutions

    4.  Design technical solution (CAD)

    5.  Model the product to create physical model - Writing documentation to
        fabricate the product

4.  Protyping (test the design, share and analyse test results)

5.  Production (make and sell the product, train people to make it)

How to propose an idea and reporting a creation
-----------------------------------------------

-   Propose an idea: Actually the simpler solution is to post an
    [issue](https://github.com/Gillou38/Drying-open-source-solution/issues).
    Once create, may be to speak about that proposition like on a forum,
    detailled it, modify it ...

-   Report a dryer: You can report dryers make with a new .odt file (1 file by
    dryer)

-   Organise different technology of dryer's components. On [state of
    art](https://github.com/Gillou38/Drying-open-source-solution/blob/master/01%20-%20Ideas%20and%20concepts/State%20of%20art.odt),
    we try to organise different components usable in a dryer, there advantages
    and there disadvantages.

How to participate in the development
-------------------------------------

It's the bigger part of the project, it begin with statement of the need, the
aim of the product and finish with prototyping documentation. Functional
analysis - Formalise technical problems : "How we want to the product work ?" :
For that we distinguish different phase : - Using phase - Clean phase ...

For each phase, we create functions which can describe precise need. Generally,
they're 3 kind of functions :

-   Principal function : that's the aim of the product, \~ Dry food

-   Using functions : that's optimisation functions for a good utilisation of
    the system, like "Be ergonomic"

-   Constraint functions : that the limit of the other functions, like "Don't
    burn food"

To develop (and propose) technical solutions, we use FAST diagrams. It's an
abstract technique to generate and organize technical functions and technical
solutions.

To choose technical solutions, we use, SADT diagrams. It's a more concrete
solution, which place each action in relation to other action, and make plan of
the process.

Prototyping
-----------

We are not so far... coming soon, hopefully!

Production
----------

We are not so far... coming soon, hopefully!

The tools we use
----------------

-   Cloud/versioning: GitHub

-   Documentation: [Libre office](http://www.libreoffice.org/)

-   CAD: [Free cad](https://freecadweb.org/)

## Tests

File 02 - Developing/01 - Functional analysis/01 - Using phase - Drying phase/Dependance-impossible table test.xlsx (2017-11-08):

Dependance table |  |  |  |  |  |  |  |  |  |  |  |  |  | Impossible table
 |  | Output dependance |  |  |  |  |  |  |  |  |  |  |  |  |  | Impossible mix
 |  | Heat module |  |  | Convection module |  |  | Deshumidifier module |  |  | Pipe module |  |  |  |  | Heat module |  |  | Convection module |  |  | Deshumidifier module |  |  | Pipe module
 |  | H1 | H2 | H3 | C1 | C2 | C3 | DH1 | DH2 | DH3 | P1 | P2 | P3 |  |  | H1 | H2 | H3 | C1 | C2 | C3 | DH1 | DH2 | DH3 | P1 | P2 | P3
Heat module | H1 Solar |  |  |  |  |  |  |  |  |  |  |  |  | Heat module | H1 Solar
 | H2 Combustion |  |  |  |  |  |  |  |  |  |  |  |  |  | H2 Combustion |  |  |  |  |  |  |  |  |  |  |  | x
 | H3 Elec |  |  |  |  |  |  |  |  |  |  |  |  |  | H3 Elec
Convection module | C1 Warm in draught |  |  |  |  |  |  |  |  |  |  |  |  | Convection module | C1 Warm in draught |  | x | x |  |  |  |  | x | x | x |  | x
 | C2 |  |  |  |  |  |  |  |  |  |  |  |  |  | C2
 | C3 Ventilator |  | x | x |  |  |  |  | x | x | x |  |  |  | C3 Ventilator
Deshumidifier module | DH1 Air Exchange |  |  |  | x |  |  |  |  |  |  |  |  | Deshumidifier module | DH1 Air Exchange |  |  |  |  |  |  |  |  |  | x |  | x
 | DH2 Condensation |  |  |  |  |  |  |  |  |  |  |  |  |  | DH2 Condensation
 | DH3 Absorption |  |  |  |  |  |  |  |  |  |  |  |  |  | DH3 Absorption |  |  |  |  |  |  |  |  |  | x
Pipe module | P1 Pipe orga |  |  |  |  |  |  |  |  |  |  |  |  | Pipe module | P1 Pipe orga |  |  |  | x |  |  | x |  | x
 | P2 Direct linked |  |  |  | x |  |  |  |  |  |  |  |  |  | P2 Direct linked
 | P3 All in drying room |  |  |  |  |  |  |  |  |  |  |  |  |  | P3 All in drying room |  | x | x | x |  |  | x

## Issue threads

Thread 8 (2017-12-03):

[Leia] Design supporting structure

jbon, 2017-12-03:
The structure supporting the towers and hosting the fans has to be designed

Gillou38, 2017-12-05:
@jbon
I add 1st version of the structure with some indications, maybe it need some modification.
I try to optimize quantity of material, but it made it more complex to built without hole.

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

Link to the file :
https://github.com/Gillou38/Drying-open-source-solution/tree/master/02%20-%20Developing/Dryer%20Le%C3%AFa

jbon, 2017-12-06:
@Gillou38 I created the 3DModel of the structure and made some drawings to explain the parameters. See here: https://github.com/jbon/Drying-open-source-solution/blob/master/02%20-%20Developing/Dryer%20Le%C3%AFa/README.md

By drawing the structure, I realized some parts of the structure you designed were redundant so I left them out (see red strokes on the figure). Please have a look at the result and tell me whether it fits your expectations.

I did not model the beams inside the drying chamber (see yellow strokes on the figure) because I am not sure how you want to attach the OSB panels to them to separate the drying columns. Do you have a idea how to do that?

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

Gillou38, 2017-12-06:
@jbon
I think the structure in 2 parts, maybe that's better to separate the 2 steps:
- 1st the exterior structure, supporting structure
- 2nd the interior structure, to fix drying columns and deshumidifier. So yellow and red strokes is only used to fix drying columns, it's like a set square but used to screw inside. The red strokes is redundant for the supporting structure, but they used to columns drying. The yellow stroke will be screw by the bottom, and the columns by the side.

I'm not sure to be clear.
If you think about something better, you're welcome.

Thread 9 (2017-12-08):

[Leila] List hardware

Gillou38, 2017-12-08:
- Before choose hardware.

- Continue and improve list of hardware :
https://github.com/Gillou38/Drying-open-source-solution/blob/master/02%20-%20Developing/Dryer%20Le%C3%AFa/Hardware.ods

- Technical requirement :
         - screen for trays : the cheaper with food grade materials
         - Resin less OSB panel: the cheaper, near Barcelonette (or Grenoble)
         - Pin beam: without treatment, the cheaper, near Barcelonette (or Grenoble), could be a board to cut
         - Ventilator: 100m^3/h
         - Rotation variator: adapt to ventilator
         - Dehumidifier: ~70L/day ; 1 000m^3/h
         - Temperature regulator: adapt to dehumidifier
         - All kind of fix system which could be useful

- Improvement:
         - Best organization
         - Add description

Gillou38, 2017-12-08:
@jbon

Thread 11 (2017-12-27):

[Leia] Problem with air flow?

jbon, 2017-12-27:
the red beams on the image may block the air flow on the front and the rear of the first and the last drawer row.

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

jbon, 2018-01-02:
there are actually 5 beams potentially either creating turbulence in the air flow or blocking its way.

Maybe it would be better to have the beam structure outside of the rooms built by the panels, instead of having them inside.

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

Gillou38, 2018-01-05:
If we use a beam with a section sizing 50 x 20, we can delete optimize it.
But It need to change the structure.

Gillou38, 2018-01-10:
I modify beam section to optimize it.

Closed 2018-01-10.

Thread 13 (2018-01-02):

[Leia] decide upon plenum design

jbon, 2018-01-02:
On the [provided sketch](https://github.com/Gillou38/Drying-open-source-solution/blob/master/02%20-%20Developing/Dryer%20Le%C3%AFa/Original%20design%20V2.jpg) specifies one plenum each 30cm, each plenum having the same orientation and size.

I doubt this is the best was to force the air flow going up in the drawer towers. I think the plenums will create turbulence and hinder good air flow. Moreover, I think the specified system will create a imbalance in air flows between the first and the last drawer tower (the first tower becomes more air than the last).

In order to support the discussion, I provided three different designs:
- one according to the provided specification: [option 1](https://github.com/jbon/Drying-open-source-solution/blob/master/02%20-%20Developing/Dryer%20Le%C3%AFa/CAD/STL%20exports/Structure_alternativePlenum1.stl)
- one with the same amount of plenums but with progressive angles. [option 2](https://github.com/jbon/Drying-open-source-solution/blob/master/02%20-%20Developing/Dryer%20Le%C3%AFa/CAD/STL%20exports/Structure.stl)
- one with only one oblique plan [option 3](https://github.com/jbon/Drying-open-source-solution/blob/master/02%20-%20Developing/Dryer%20Le%C3%AFa/CAD/STL%20exports/Structure_alternativePlenum2.stl)

I think the option 2 is the best, because there is no turbulence created, the air flow will be smoothly distributed among all towers, and it is easy to fabricate.

Gillou38, 2018-01-05:
I think option 2 and 3 work.
option 3 : maybe the best but, I'm not sure, very regularly and easy to make.
option 2 : create more turbulence, and could increase efficiency, I'm not sure.

Gillou38, 2018-01-18:
Option 3 doesn't work. Need to break the airflow.

"Honnêtement je n'y crois pas trop. Pour le bas tu ne casses pas le flux
pour qu'il se répartisse de manière homogène, il est juste guidé, la
première armoire n'aura pas grand chose et peut être aussi la deuxième"

Best solution is 2.

Closed 2018-01-18.

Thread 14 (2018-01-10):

[Leïa] Fabrication - Nomenclature and quantity of wood

Gillou38, 2018-01-10:
Make (or adapt) spreadsheet to calculate quantity of wood automatically.

In a 1st time, make the nomenclature of plane (raboté) wood.
In a 2nd time, make the nomenclature of not plane wood, and if we buy board.

Gillou38, 2018-01-10:
Think about technical to make layout (calepinage) of panel.
Before I use Opticut (a soft) but it can't using scalable design.

How make a functional spreadsheet for that step ?

Gillou38, 2018-01-10:
Inspiration :
https://www.lairdubois.fr/blog/56-un-autre-plugin-sketchup-pour-les-fiches-de-debit.html
http://www.metabricoleur.com/t12683p25-sketchup-un-autre-plugin-pour-les-fiches-de-debit

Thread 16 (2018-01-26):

[Leïa] Fabrication's instruction

Gillou38, 2018-01-26:
Make the fabrication's instruction (libreOffice).

- Write text
- make it and take photos
- insert photo

Gillou38, 2018-02-02:
Detail of the text :
I) Global vision
Difficulty ...
II) Fabrication
- Beam
- Panel
III) Assembly
- Global structure
- Plenum
- Panel
- Drawers
- Drawers support
- Dehumidifier support
- Doors
IV) Drawings

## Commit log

2017-11-09 Passage sur sourcetree
    [Dependance-impossible table test.xlsx]
2017-12-01 first draft Dryer Leïa
    [Dryer_Leïa.FCStd, Dryer_Leïa.stl]
2017-12-01 minor corrections docs dryer leïa
    [Dryer_Leïa.FCStd]
2017-12-01 parametrized number rows/columns
    [Dryer_Leïa.FCStd]
2017-12-05 redesign drawer with new material requirements
    - OSB plates
    - corner beams
    [Dryer_Leïa.FCStd]
2017-12-05 redesign drawer with new material requirements
    [Dryer_Leïa.FCStd]
2017-12-05 export STL and clean
    [Drawer.stl, Dryer_Leïa.FCStd, Dryer_Leïa.stl]
2017-12-05 updated drawer design
    [Drawer.stl, Dryer_Leïa.FCStd]
2017-12-06 create dryer structure
    [Drawer.stl, Dryer_Leïa.FCStd, Dryer_Leïa_bkp.FCStd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]
2017-12-08 Add hardware list of materials
    [Hardware.ods]
2017-12-08 Update Hardware
    [Hardware.ods]
2017-12-13 redesign drawer towers
    [Dryer_Leïa.FCStd]
2017-12-13 update design drawer towers
    [Dryer_Leïa.FCStd]
2017-12-13 update drawings according to new design
    [Full assembly.stl, Structure.stl]
2017-12-13 correct materials in drawing structure
2017-12-14 optimize design drawer towers
    [Dryer_Leïa.FCStd, Fastener_double_L.FCStd, Full assembly.stl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]
2017-12-15 add fasteners to drawer towers
    [Drawer_beam_sized_L_fastener.stl, Dryer_Leïa.FCStd, Full assembly.stl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]
2017-12-15 clean parameter spreadsheet in CADModel
    [Dryer_Leïa.FCStd]
2018-01-03 structure hat design
    - inclined side and longitudinal panels drawn
    - still one panel to be designed (top panel)
    - was not able to calculate angles to all parts fit together
    [Dryer_Leïa.FCStd, Full assembly.stl, Structure.stl]
2018-01-03 structure hat design V2
    - with right angles
    - with all panels
    [Dryer_Leïa.FCStd, Full assembly.stl, Structure.stl]
2018-01-03 [hat design] corrected some parameters and values
    [Dryer_Leïa.FCStd, Full assembly.stl, Structure.stl]
2018-01-03 corrected size of side room
    [Dryer_Leïa.FCStd]
2018-01-03 first draft plenums
    [Dryer_Leïa.FCStd, Full assembly.stl, Structure.stl]
2018-01-03 add side room floor
    [Dryer_Leïa.FCStd]
2018-01-03 proposition of alternative designs for plenums
    [Dryer_Leïa_alternativePlenums1.FCStd, Dryer_Leïa_alternativePlenums2.FCStd, Structure_alternativePlenum1.stl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]
2018-01-03 Update upper_room_proposition
    [Dryer_Leïa_upper_room_proposition.FCStd]
2018-01-05 Add doors, handles and locking
    [Dryer_Leïa_complete.FCStd]
2018-01-09 Add doors, reduce wood quantity, renforced structure
    [Dryer_Leïa_renforced.FCStd]
2018-01-10 Beginning bill of materials
    [Dryer_Leïa_renforced.FCStd]
2018-06-07 Big update V2 of CAD
    [Dryer_Leïa_complete.FCStd, Dryer_Leïa_upper_room_proposition.FCStd, Hardware.ods]
